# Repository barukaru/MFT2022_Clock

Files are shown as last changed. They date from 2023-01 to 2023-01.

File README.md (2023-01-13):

# MFT2022_Clock
Maker Fair Tokyo2022で出展販売したローリングクロックのデータ保存場所  

～フォルダ/ファイル説明～  
/3D_Laser_cutter																：外装（レーザーカッター加工データ）  
/3D_printer(FDM)																：本体（3Dプリンタ出力データ）  
20221019_step_motor_SW_use_(intrpt-timer).py		：プログラム（Python）  
README.md																				：本ファイル  
assembling instructions.pdf											：外装と本体の組立手順  
step_motor_cirkit_ブレッドボード.pdf							：ブレットボード配線図  
step_motor_cirkit_回路図.pdf											：回路図  
ローリングクロックプログラム説明書(timer割込み.pdf	：プログラム説明書  

【参考】  
本プログラムは以下の構成で実施しています  
制御基板：RaspberryPi pico（MicroPython）
モーター：ステッピングモータ”28BYJ-48”  
ドライバ：ULN2003  
※モーターとドライバのセット品をAliExpressで購入

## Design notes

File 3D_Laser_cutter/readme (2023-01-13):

レーザーカッターで作成するローリングクロックの外装データ  

ファイル名が組立手順書の品番とリンク  
../assembling instructions.pdf

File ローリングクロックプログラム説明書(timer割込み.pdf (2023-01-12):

## ～ローリングクロック プログラム説明書～

お買い上げいただきありがとうございます。
本書では付属しているモータで時計を動作させるためのプラグラム例を解説しています。 「とりあえず動いているところを見てみたい！」という方は是非読んでみてください。

本プログラムは以下の環境で動作確認をしています。

- マイコンボード ： Raspberry Pi Pico
- ファームウェア ： MicroPython（v1.19.1.uf2）
- プログラム言語 ： Python 3.7.9
- 開発環境 ： Windows10、Thonny（Ver.3.3.13）

はじめに

プログラム

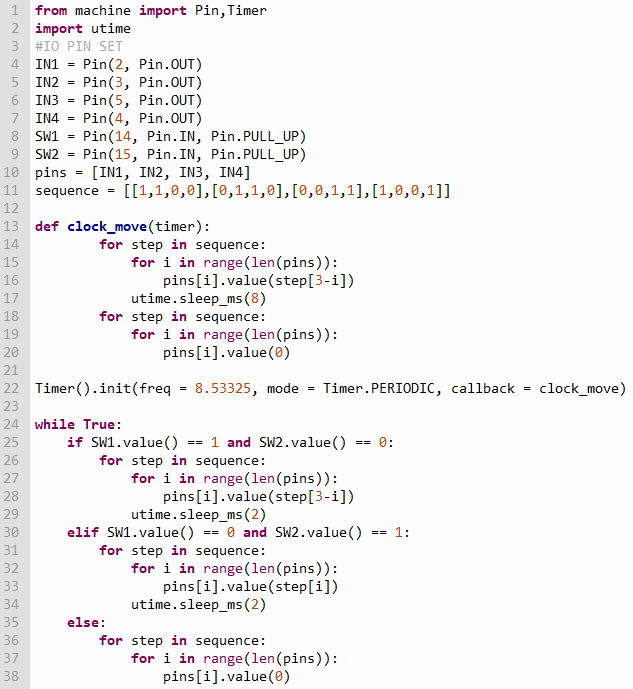
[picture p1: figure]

本プログラムの役割ブロックごとに説明をしていきます。

1～2 行目で動作に必要なモジュール（ライブラリ）の読み込みを行います。
1 行目は、machine モジュール内の I/O ピン制御を使うため、クラス Pin をロードする。 また、同モジュール内のタイマ割り込みも使うため、クラス Timer もロードする。
2 行目は、時計の要となる utime モジュールをロードする。

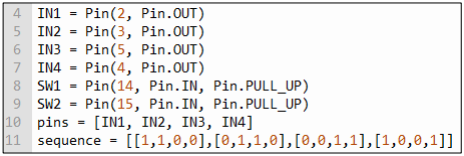
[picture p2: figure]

4～7 行目で先ほど読み込んだクラス Pin を用いて、2～5pin を出力設定にし、
8～9 行目で、14pin と 15pin を入力設定にする。
10 行目は、変数 IN1～4 を後に繰り返し処理しやすいように配列としてまとめている。 11 行目は、励磁させるコイルごとの High/Low の組み合わせを配列としてまとめている。

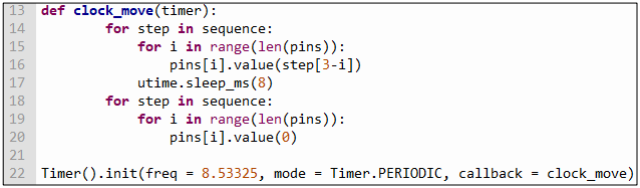
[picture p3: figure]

13～22 行目はステッピングモータの正転動作を制御しているプログラムとなる。
13～20 行目で、clock_move 関数を定義しており、22 行目で 8.53325Hz ごとに clock_move 関数を タイマ割り込みで呼び出すための設定となる。関数の詳細は以下の通りとなる。
1. for 文が開始されると、まず step に配列 sequence の最初の要素である[1,1,0,0]が入る。
2. その後、中の for 文が開始、i に 0 が入り、pins[0] = IN1、step[3] = 0 のため IN1=0 となる。 繰り返しが終わると、IN1＝0、IN2＝0、IN3＝1、IN4＝1 という組み合わせになる。
3. 最後に 5ms スリープが入り、配列 sequence の次の要素に進み、要素数分１～2 を繰り返す。
4. 18～20 行目の for 文はすべて Low 出力として、時間が進まない休み区間となる。（モータの発 熱防止のため）

プログラム説明

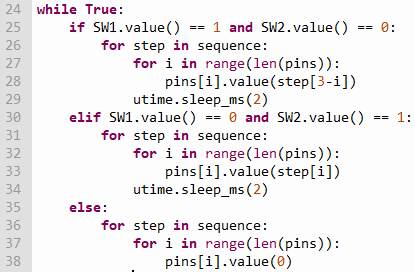
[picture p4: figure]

24～38 行目は、時刻調整用のプログラム部分となる。
14pin と 15pin に接続しているスイッチ ON/OFF の組み合わせによって、ステッピングモータを任 意の方向に通常動作より速く回転させ、時刻の調整ができる。

【14pin＝ON、15pin＝OFF（25～29 行目）】
14pin のスイッチを押している間、ステッピングモータが正転（時間が進む）方向に回る。
for 文の制御部分に関しては、前ページにある clock_move 関数のスリープ時間を短くしたものなの で、説明は割愛する。

【14pin＝OFF、15pin＝ON（30～34 行目）】
15pin のスイッチを押している間、ステッピングモータが逆転（時間が戻る）方向に回る。 基本的な流れは clock_move 関数と同じだが、逆方向に回転させるため 33 行目の value の引数を step[i]に変更している。

【14pin＝OFF、15pin＝OFF or 14pin＝ON、15pin＝ON（35～38 行目）】
14pin と 15pin のスイッチがどちらも押されていない場合、もしくは両方とも押している間、ステッピン グモータは停止する。（モータの発熱防止のため）

いかがでしたでしょうか。問題なく動かすことは出来ましたか？ 拙い説明で分かりづらい部分はあったかと思いますが、楽しんでもらえていたら嬉しいです。 その他にも動かす方法はたくさんあると思いますので、色々と試してみてください。 それでは、またどこかで。一緒に楽しい電子工作ライフを歩みましょう！
以上

最後に

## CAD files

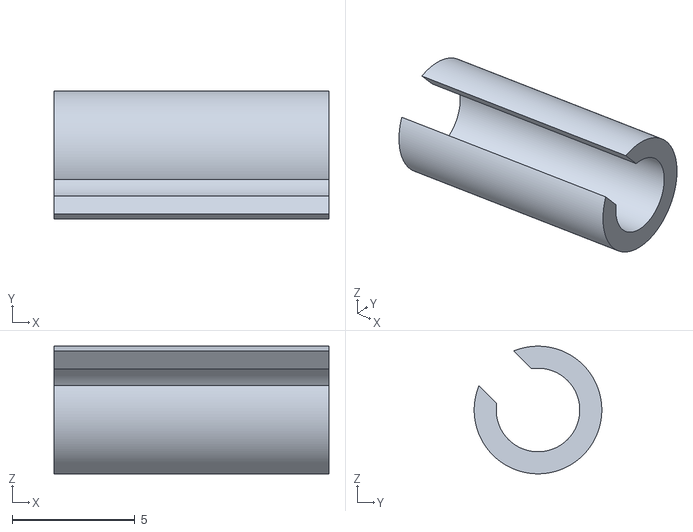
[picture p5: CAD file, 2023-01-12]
3D_printer(FDM)/sec_shaft_stopper.stl
11.2 x 5.20 x 5.20

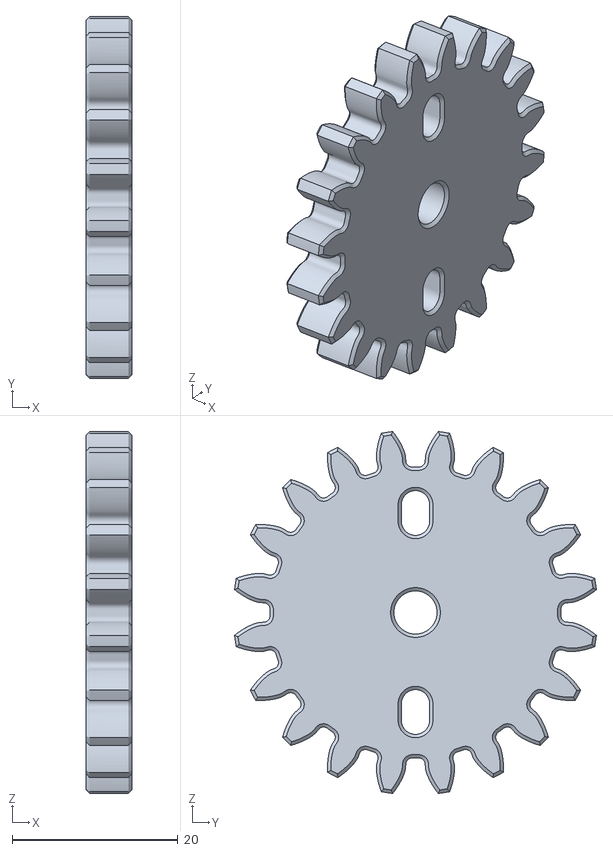
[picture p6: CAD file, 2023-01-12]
3D_printer(FDM)/gear_min1_1.stl
5.50 x 43.7 x 43.7

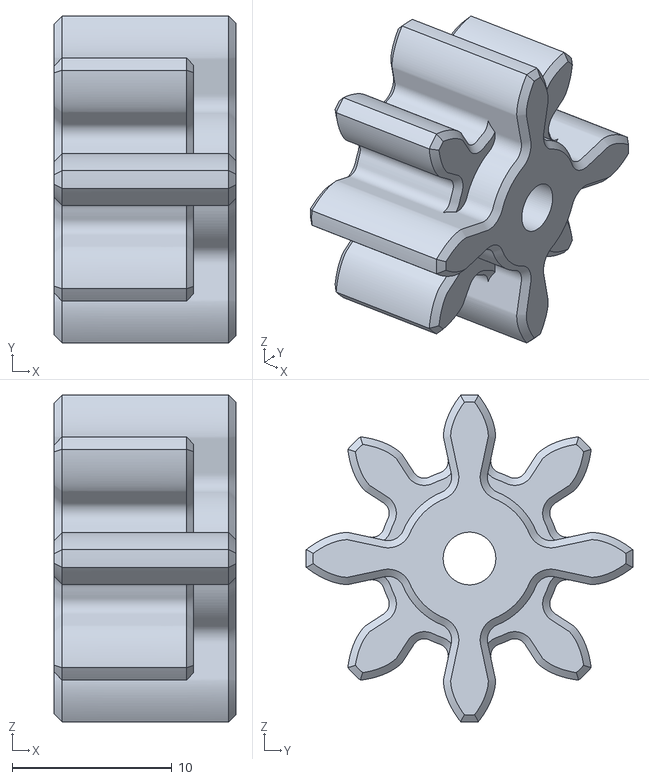
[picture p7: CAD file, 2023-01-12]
3D_printer(FDM)/link_gear(min1-min2).stl
11.4 x 20.5 x 20.5

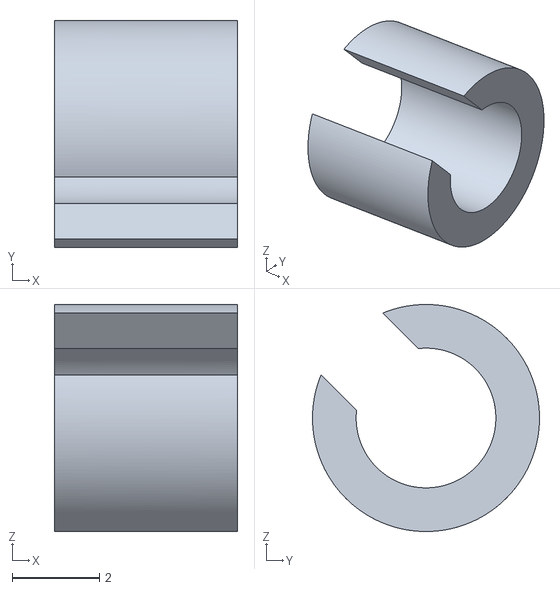
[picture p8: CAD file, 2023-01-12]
3D_printer(FDM)/hour_shaft_stopper.stl
4.20 x 5.20 x 5.20

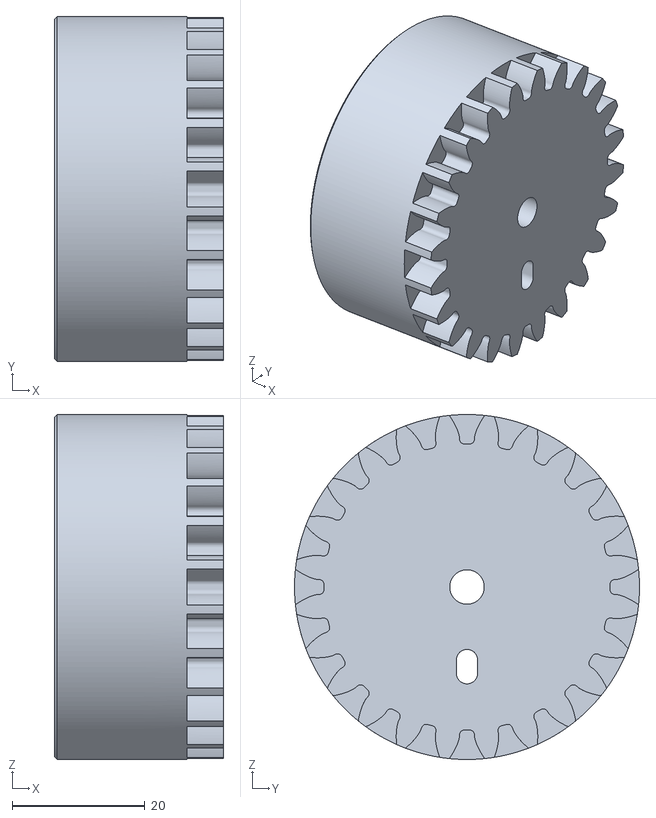
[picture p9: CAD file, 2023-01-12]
3D_printer(FDM)/gear_hour.stl
25.5 x 52.0 x 52.0

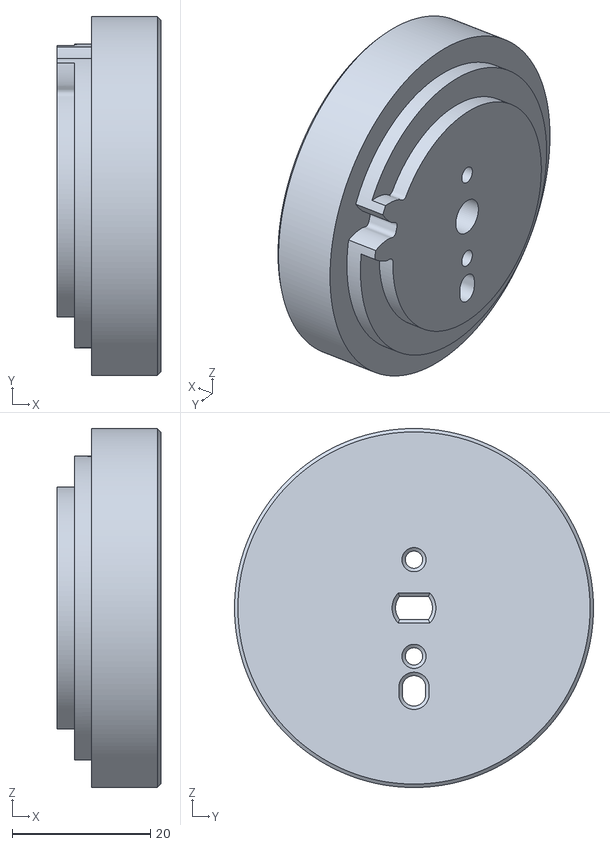
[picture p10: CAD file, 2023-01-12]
3D_printer(FDM)/gear_sec.stl
15.0 x 52.0 x 52.0

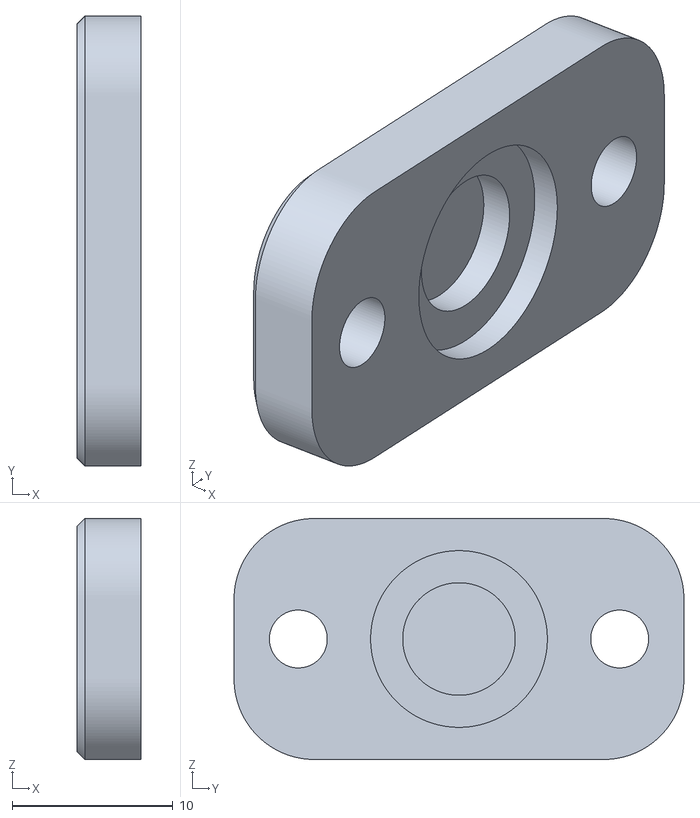
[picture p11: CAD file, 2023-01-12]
3D_printer(FDM)/shaft_stopper.stl
4.00 x 28.0 x 15.0

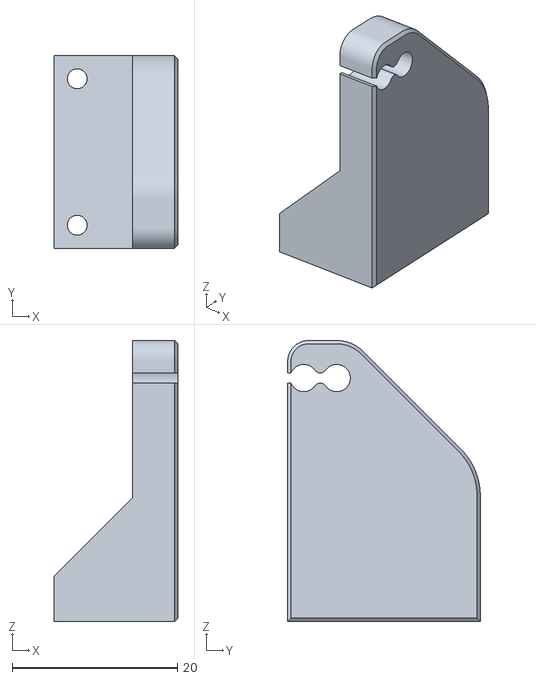
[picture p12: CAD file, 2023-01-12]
3D_printer(FDM)/shaft_holder.stl
15.0 x 23.4 x 34.1

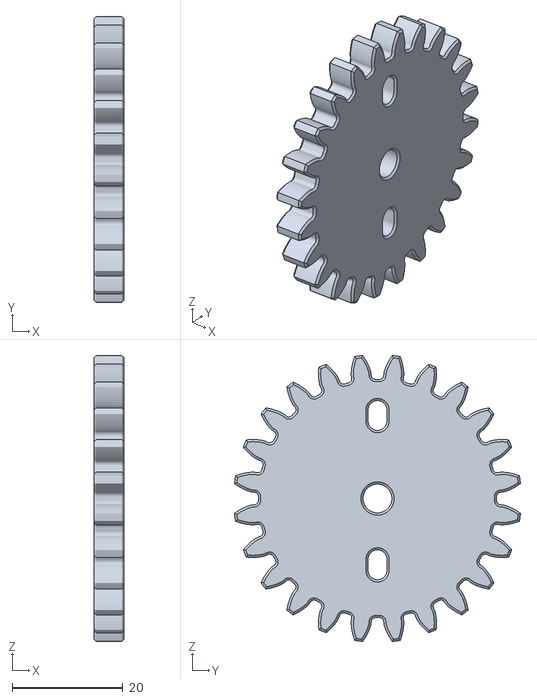
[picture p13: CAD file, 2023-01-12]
3D_printer(FDM)/gear_min2_1.stl
5.50 x 51.7 x 51.7

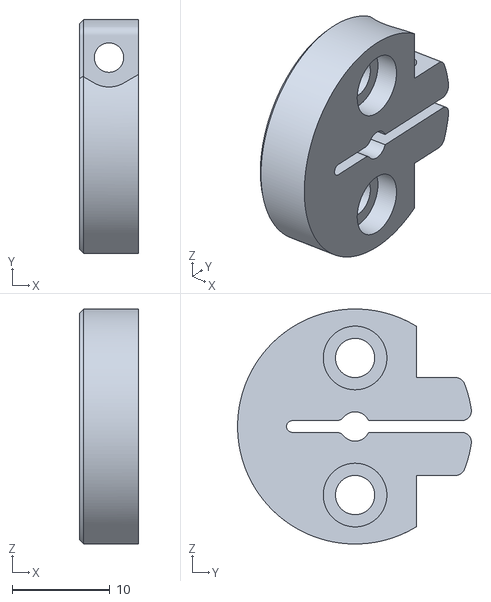
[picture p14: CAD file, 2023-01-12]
3D_printer(FDM)/set_collar.stl
6.00 x 23.9 x 24.0

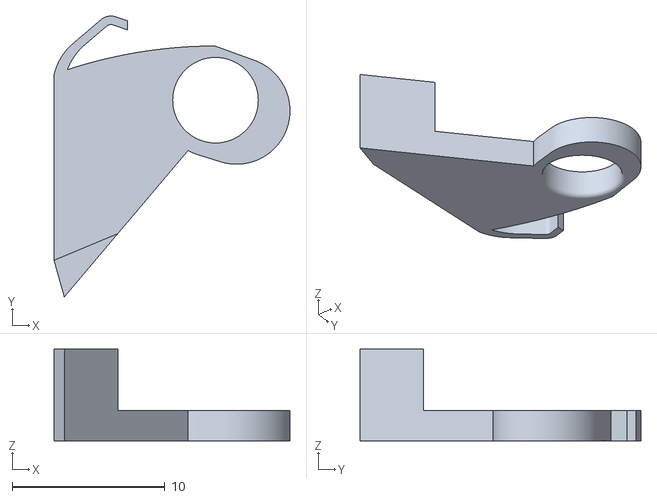
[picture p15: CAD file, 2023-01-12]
3D_printer(FDM)/test_tsume.stl
15.4 x 18.4 x 6.00

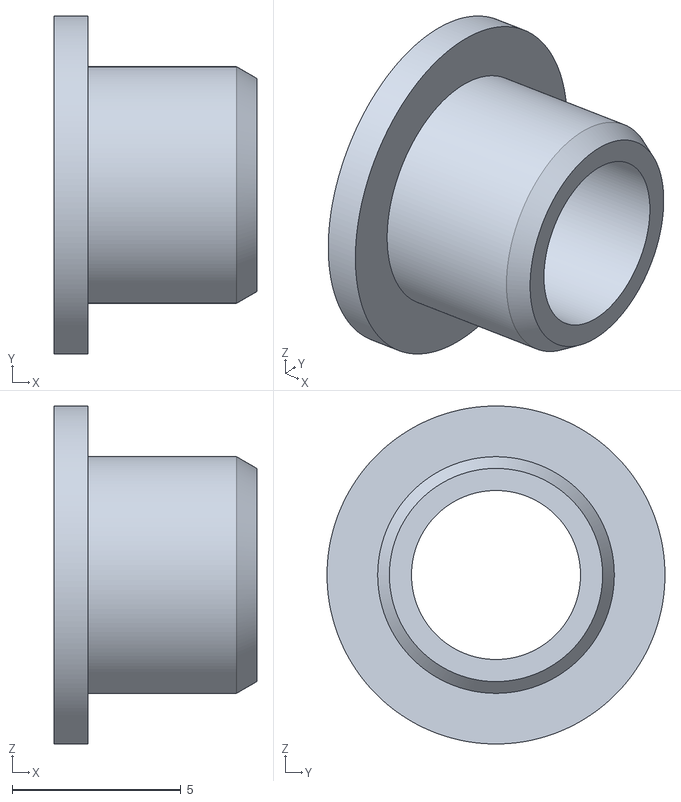
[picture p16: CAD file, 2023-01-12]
3D_printer(FDM)/bush.stl
6.00 x 10.0 x 10.0

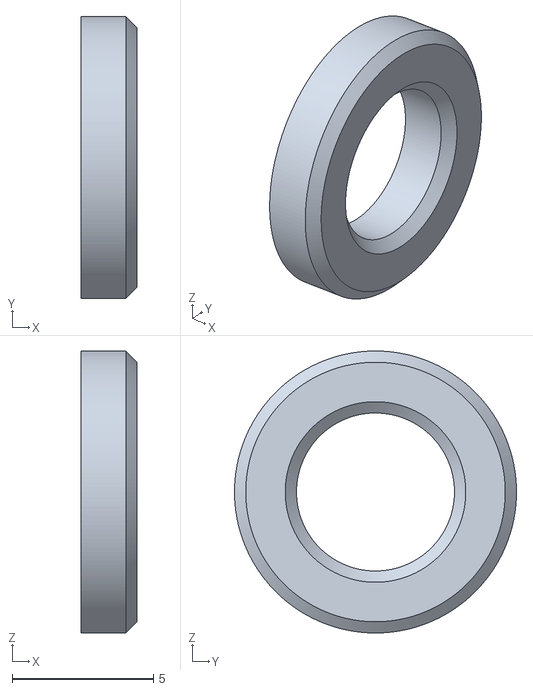
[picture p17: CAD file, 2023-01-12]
3D_printer(FDM)/washer.stl
2.00 x 10.0 x 10.00

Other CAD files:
3D_printer(FDM)/gear_min2_2.stl
3D_printer(FDM)/gear_min1_2.stl

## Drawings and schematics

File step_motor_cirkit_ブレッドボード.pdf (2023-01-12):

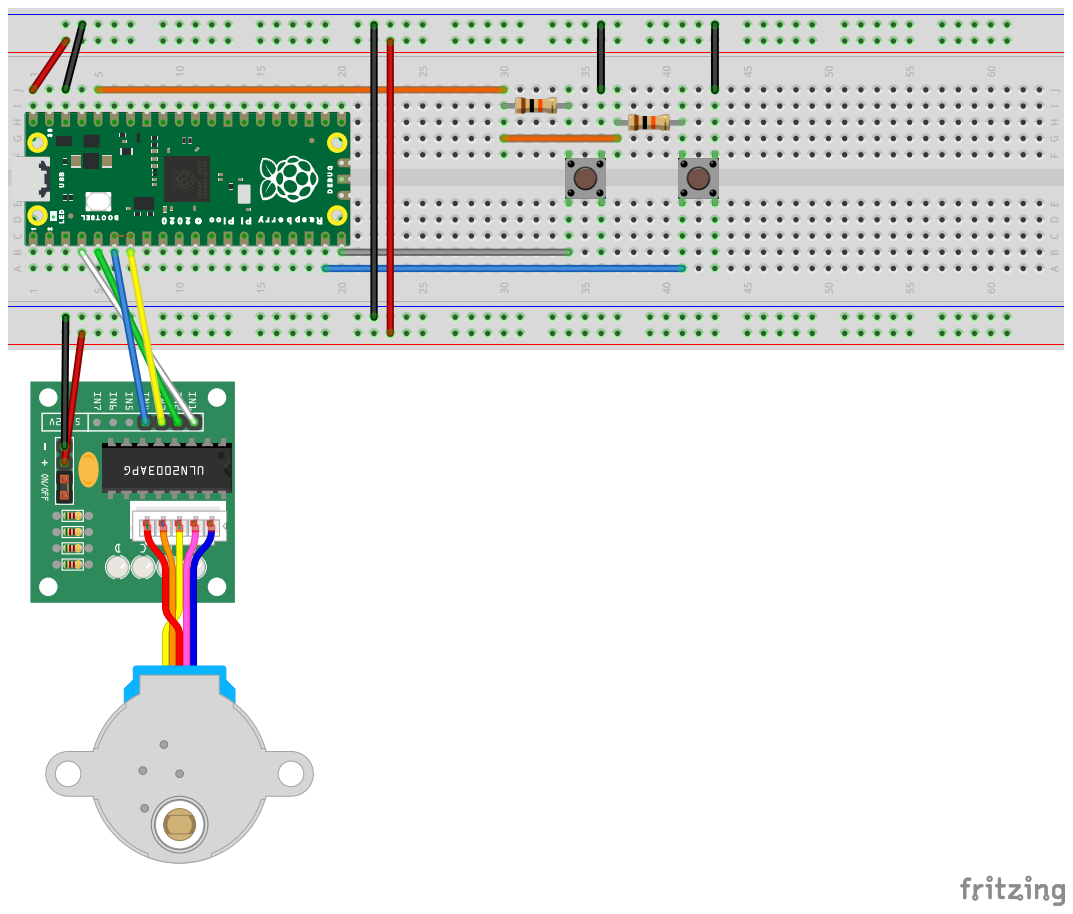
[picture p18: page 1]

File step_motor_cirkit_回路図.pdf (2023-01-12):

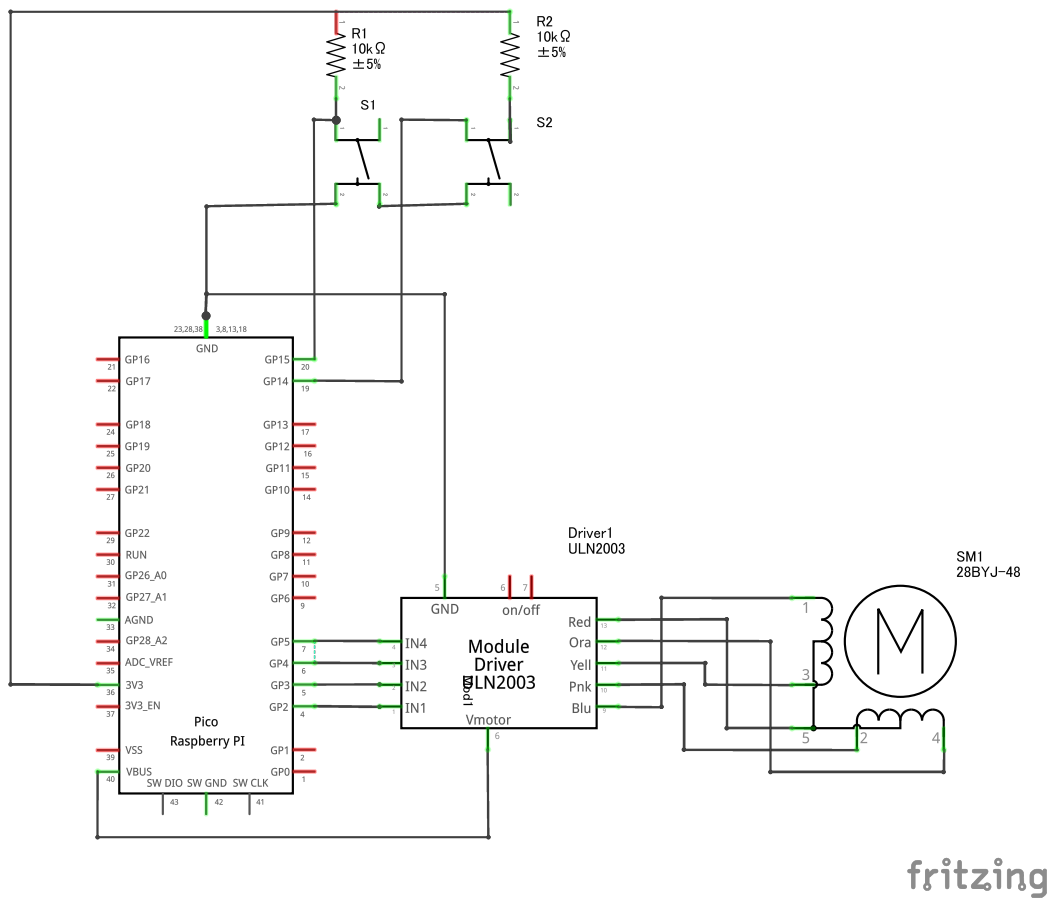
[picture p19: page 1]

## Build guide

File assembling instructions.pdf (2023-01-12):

1 / 2

# ＜Counter Clock 組立手順書＞

◆パーツリスト

品番 | パーツ名称 | 数量 | 品番 | パーツ名称 | 数量 | 品番 | パーツ名称 | 数量
1 | gear_sec | 1 | 9 | plate_base | 1 | 17 | Bush | 1
2 | gear_min1 | 1 | 10 | plate_L | 1 | 18 | - | -
3 | gear_min2 | 1 | 11 | Shaft_sub2 | 1 | 19 | Shaft stopper | 1
4 | gear_h | 1 | 12 | plate_R | 1 | 20 | Bracket | 2
5 | link gear | 3 | 13 | Cover | 1 | 21 | Cover stopper | 4
6 | Shaft_main | 1 | 14 | shaft holder | 1 | 22 | Washer_M5 | 1
7 | Shaft_sub1 | 1 | 15 | Washer_t2 | 3 | 23 | Spacer_t3.6 | 2
8 | set collar | 2 | 16 | step-motor | 1 | 24 | ネジ 3×8 | 18

◆組立工程
1. ベースプレートへの部品取り付け
2.モーターの取り付け
3.時間表示部の取り付け
4.中間ギアの取り付け

◆組立工程（詳細）
1. ベースプレートへの部品取り付け

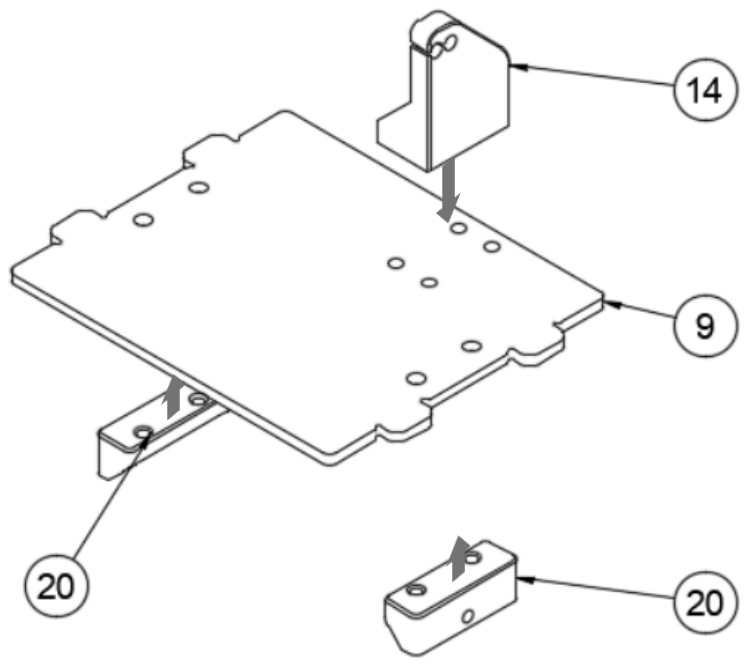
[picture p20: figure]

＜注意点＞
１．部品の取り付け向きに注意。

２．⑳bracket を⑨plate base に
取り付ける際は端面を揃える。

＜使用ネジ＞
タッピング 3×8：8 本

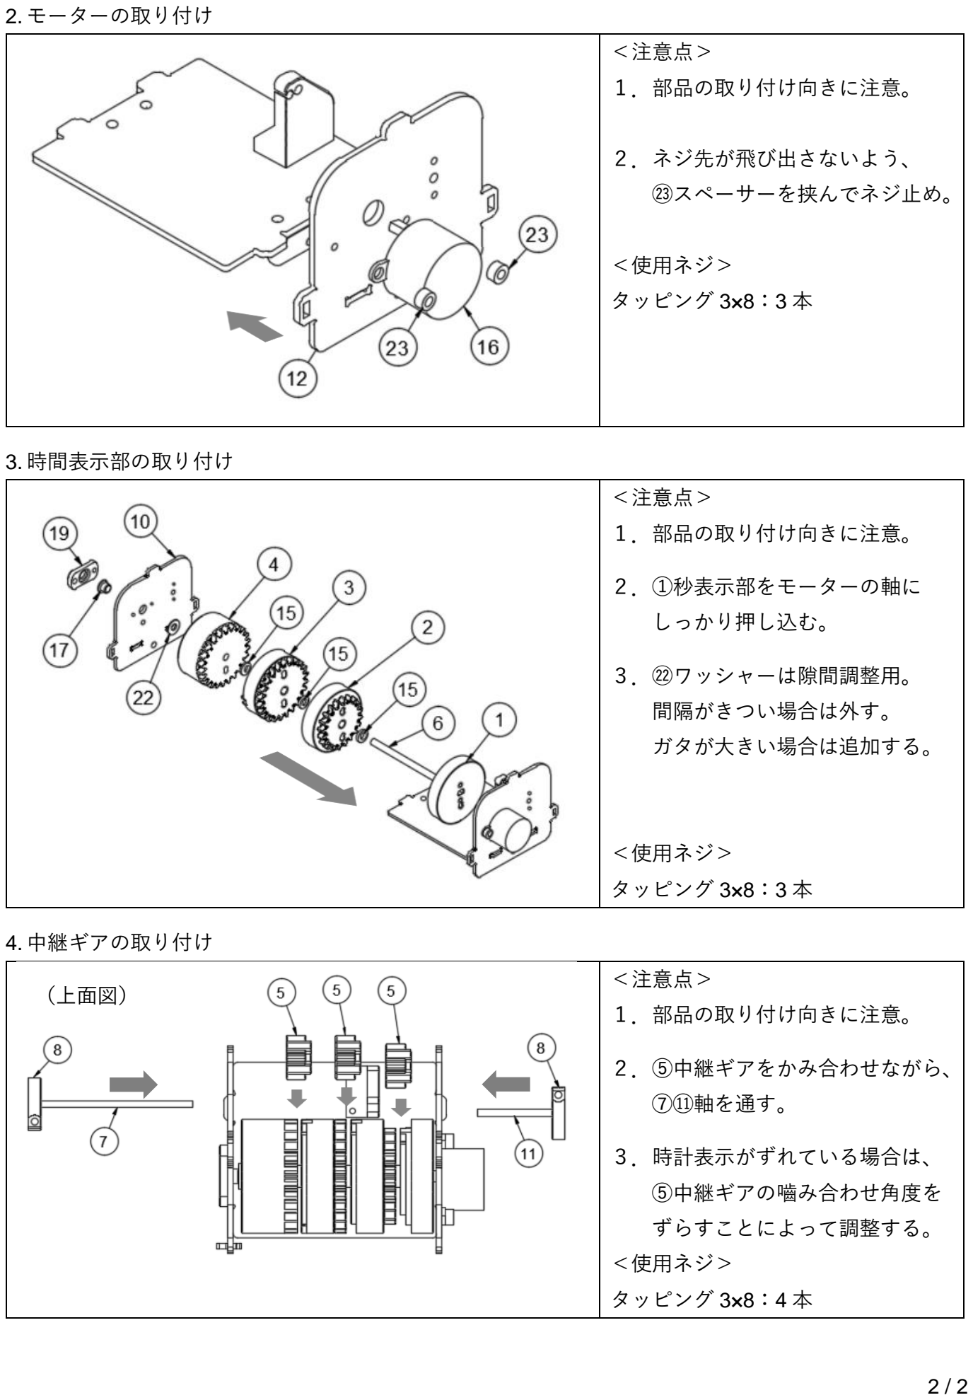
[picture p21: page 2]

2 / 2

2. モーターの取り付け

＜注意点＞
１．部品の取り付け向きに注意。

２．ネジ先が飛び出さないよう、
㉓スペーサーを挟んでネジ止め。

＜使用ネジ＞
タッピング 3×8：3 本
3. 時間表示部の取り付け
＜注意点＞
１．部品の取り付け向きに注意。

２．①秒表示部をモーターの軸に
しっかり押し込む。

３．㉒ワッシャーは隙間調整用。
間隔がきつい場合は外す。
ガタが大きい場合は追加する。

＜使用ネジ＞
タッピング 3×8：3 本
4. 中継ギアの取り付け

＜注意点＞
１．部品の取り付け向きに注意。

２．⑤中継ギアをかみ合わせながら、
⑦⑪軸を通す。

３．時計表示がずれている場合は、
⑤中継ギアの嚙み合わせ角度を
ずらすことによって調整する。
＜使用ネジ＞
タッピング 3×8：4 本

（上面図）

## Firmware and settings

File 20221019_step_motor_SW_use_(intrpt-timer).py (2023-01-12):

from machine import Pin,Timer
import utime
#IO PIN SET
IN1 = Pin(2, Pin.OUT)
IN2 = Pin(3, Pin.OUT)
IN3 = Pin(5, Pin.OUT)
IN4 = Pin(4, Pin.OUT)
SW1 = Pin(14, Pin.IN, Pin.PULL_UP)
SW2 = Pin(15, Pin.IN, Pin.PULL_UP)
pins = [IN1, IN2, IN3, IN4]
sequence = [[1,1,0,0],[0,1,1,0],[0,0,1,1],[1,0,0,1]]

def clock_move(timer):
        for step in sequence:
            for i in range(len(pins)):
                pins[i].value(step[3-i])
            utime.sleep_ms(8)
        for step in sequence:
            for i in range(len(pins)):
                pins[i].value(0)
               
Timer().init(freq = 8.53325, mode = Timer.PERIODIC, callback = clock_move) 

while True:
    if SW1.value() == 1 and SW2.value() == 0:
        for step in sequence:
            for i in range(len(pins)):
                pins[i].value(step[3-i])
            utime.sleep_ms(2)
    elif SW1.value() == 0 and SW2.value() == 1:
        for step in sequence:
            for i in range(len(pins)):
                pins[i].value(step[i])
            utime.sleep_ms(2)
    else:
        for step in sequence:
            for i in range(len(pins)):
                pins[i].value(0)        
            
            
